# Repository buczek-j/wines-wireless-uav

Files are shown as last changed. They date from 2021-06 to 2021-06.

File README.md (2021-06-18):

# wines-wireless-uav
Public Repo for Publication "What is A Wireless UAV?A Design Blueprint for 6G Flying Wireless Nodes"



## Setup 
### UAV Parts list

The list of the off-the-shelf components used in the design of our UAV include:

* [Motors: T-Motor MN501-S KV240](https://store-en.tmotor.com/goods.php?id=695)
* [Propellers: T-Motor G20x6.5](https://store-en.tmotor.com/goods.php?id=496)
* [ESCs: T-Motor FLAME 60A 12S ](https://store-en.tmotor.com/goods.php?id=370)
* [Frame: Iflight iXC15 950mm](https://shop.iflight-rc.com/index.php?route=product/product&path=25&product_id=695)
* [Flight Controller: Holybro Pixhawk Mini](http://www.holybro.com/product/pixhawk-mini/)
* [Batteries: 4S 6000mAh (2 in series for 8s)](https://www.amazon.com/HOOVO-Connector-Airplane-Helicopter-Quadcopter/dp/B07PDPGFQY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)
* [Radio Reciever: FrSky XM+](https://www.amazon.com/FrSky-Range-Receiver-Failsafe-Support/dp/B073PXL55X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)
* [Radio Transmitter: FrSky Q9 Lite](https://www.amazon.com/FrSky-Transmitter-Protocol-Airplane-Helicopter/dp/B07RQ5BCNG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)
* [NUC: NUC7i7DNK1E](https://www.amazon.com/Intel-Business-Mini-Technology-BLKNUC7i7DNK1E/dp/B07BR7LK7C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)
* [Wireless USB Adapter](https://www.amazon.com/Panda-Wireless-PAU06-300Mbps-Adapter/dp/B00JDVRCI0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)
* [Router](https://www.amazon.com/Panda-Wireless-PAU06-300Mbps-Adapter/dp/B00JDVRCI0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)
* [SDR: USRP B210](https://www.ettus.com/all-products/ub210-kit/)
* [TPU 3D filament](https://www.amazon.com/PolyFlex-3-00-mm-750g-Yellow/dp/B00YXBO1UW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)
* [Nylon Bridge 3d filament](https://www.amazon.com/Printer-Filament-1-75mm-Dimensional-Accuracy/dp/B01MXDJ3IL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)
* [3D Printer](https://www.amazon.com/LulzBot-B07PFQQSR9-TAZ-Workhorse-Edition/dp/B07PFQQSR9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)

### Construction


### Nuc Setup

### Flight Code

The flight code used for these UAVs is located [here](https://github.com/buczek-j/BasicArducopter/tree/wines-powertest). It uses the Dronekit python library to connect to the UAV via Mavlink messages. 

## Design Validation
### UAV Endurance Testing
For the endurance testing, [this script](https://github.com/buczek-j/BasicArducopter/blob/wines-powertest/power_test.py) was used to automate the process. The enduracne test outlined in the script is shown below:

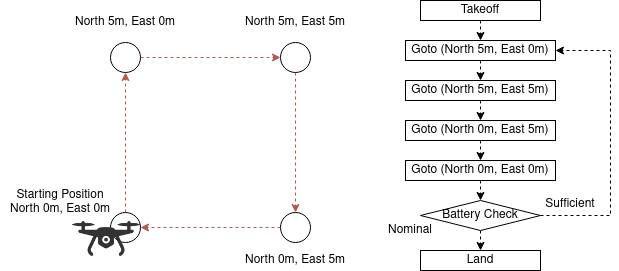
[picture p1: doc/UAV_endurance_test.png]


The UAV took off, performed a loop, and checked if its battery was below the 8S LiPo nominal voltage of 28.8V. If the voltage was below nominal, then the UAV would land, otherwise, it continued for another loop. The flight time and battery capacities were recorded and the capacities were confirmed via charging again. These values were used to calculate the total flight time of the UAV.

This process was repeated for multiple payload weights.

 This method of testing is more accurate to determine the flight time of a UAV as the UAV was contantly in motion. A flight test that would have the UAV hover in place would most likely dislpay an even longer flight time as the UAV would not need to adjust motor speeds for motion or altitude changes. 

### UAV GPS Interference
To determine the GPS interference caused by external electronics, the Pixhawk logs were analyzed. For each electronics and sheilding configuration, the UAV was armed on the ground, we waited until the desired time passed, and then the UAV was disarmed. The order of the configurations was recorded. After testing, the log files of the Pixhawk were [downloaded](https://ardupilot.org/copter/docs/common-downloading-and-analyzing-data-logs-in-mission-planner.html) from the UAV and using mission planner, .MAT files were generated from the logs. The .MAT files were parsed based on the Arming and Disarming messages and the Horizonal Dilution of Position (HDOP) of each configuration was separated. For our analysis, the HDOP recordings throughout each configuration's testing interval were averaged and the averaged HDOPs were compared. Four our testing, interval periods of 3 minutes were used. The script that we used to parse the .MAT files was [TODO]().

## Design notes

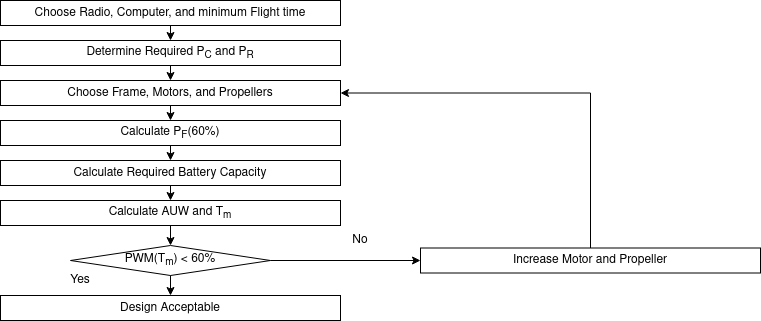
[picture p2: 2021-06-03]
doc/UAV_Deisgn_Process.png

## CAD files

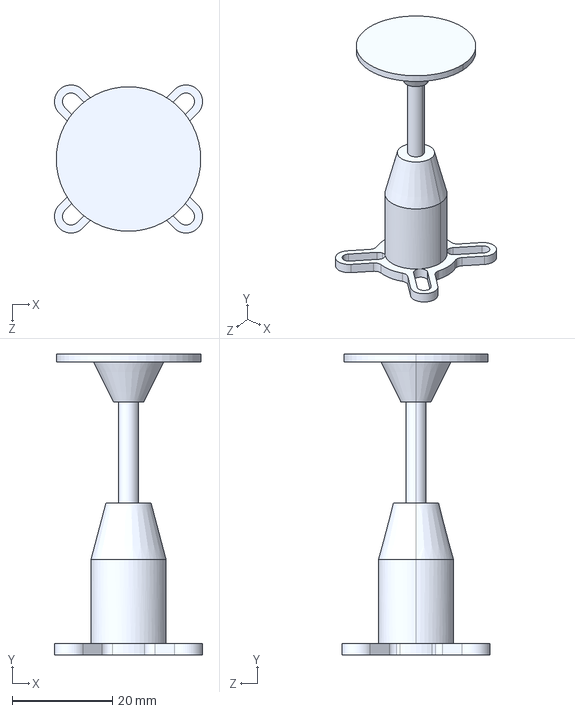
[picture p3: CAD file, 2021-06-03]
3D_Printed_Parts/Step_files/PX4_GPS_&_Compass_mast.STEP
29.5 x 60.0 x 29.5 mm

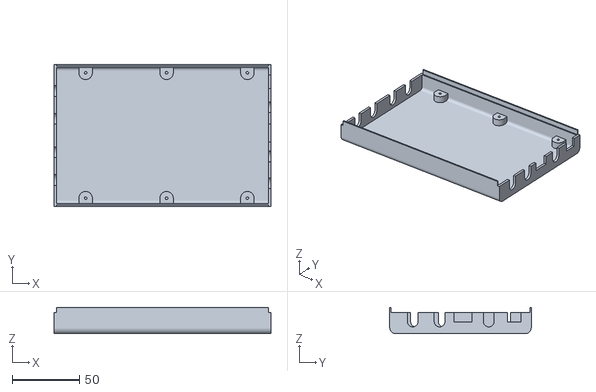
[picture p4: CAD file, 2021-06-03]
3D_Printed_Parts/STLs/bottom_case_b210.stl
161.0 x 105.0 x 19.5

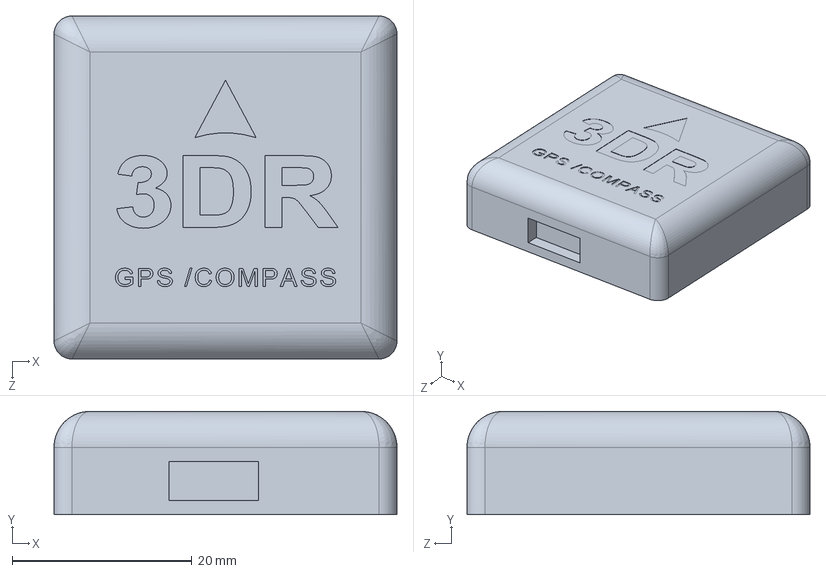
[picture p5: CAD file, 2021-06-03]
3D_Printed_Parts/Step_files/3DR_GPS_Compass.STEP
38.2 x 11.5 x 38.2 mm

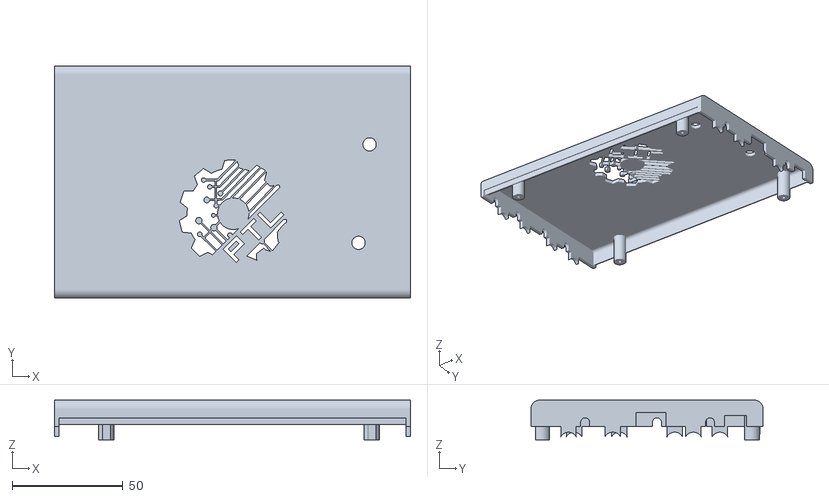
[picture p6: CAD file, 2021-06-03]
3D_Printed_Parts/STLs/top_case_b210.stl
161.0 x 105.0 x 18.0

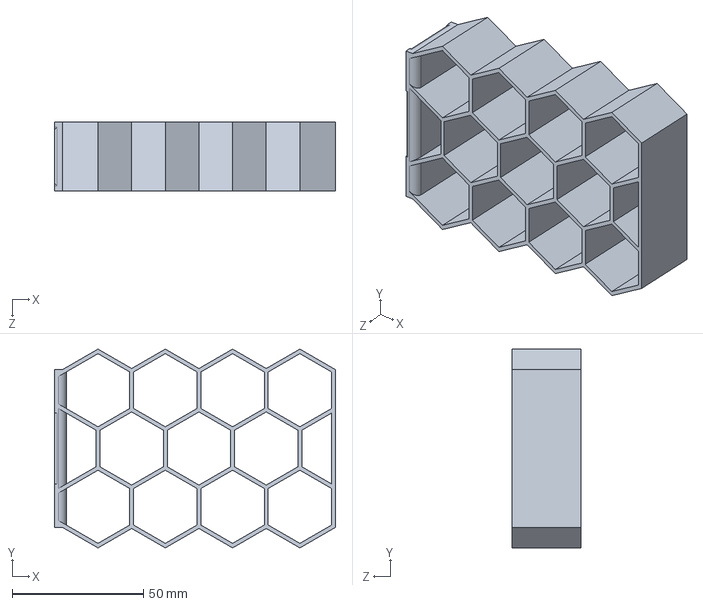
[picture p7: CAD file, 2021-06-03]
3D_Printed_Parts/Solidworks_parts/iflight_landing_gear_ziptie.SLDPRT
106.9 x 75.6 x 26.3 mm

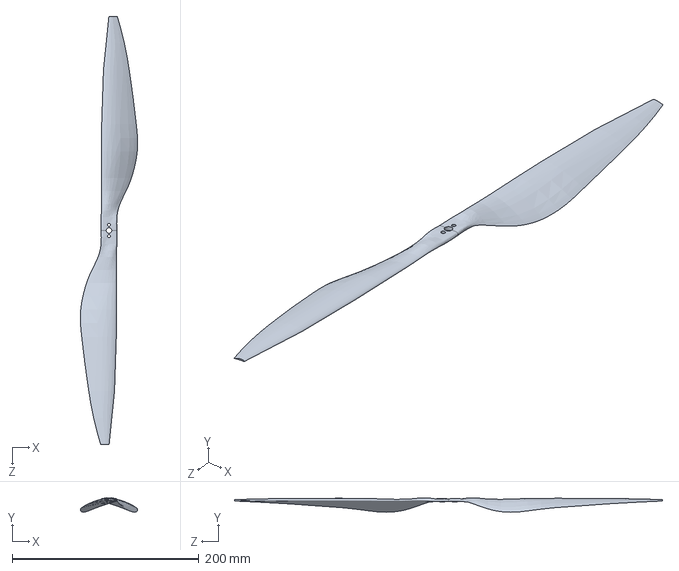
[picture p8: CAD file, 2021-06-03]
3D_Printed_Parts/Step_files/18x6.1.SLDPRT
61.4 x 15.5 x 458.0 mm

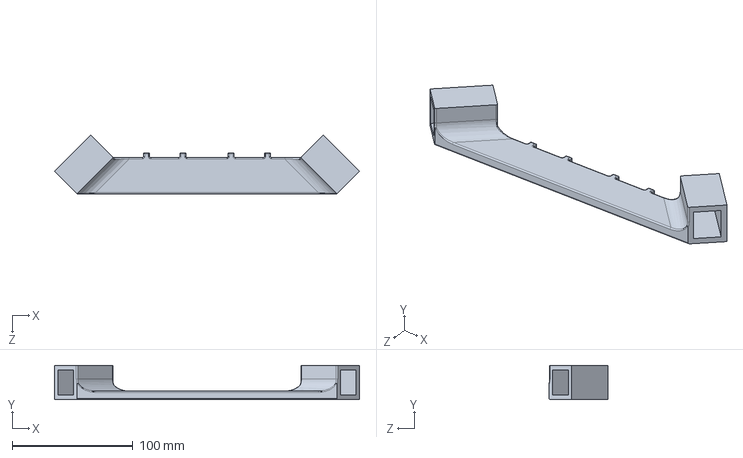
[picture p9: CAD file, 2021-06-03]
3D_Printed_Parts/Solidworks_parts/iflight_battery_mount.SLDPRT
252.3 x 28.3 x 48.7 mm

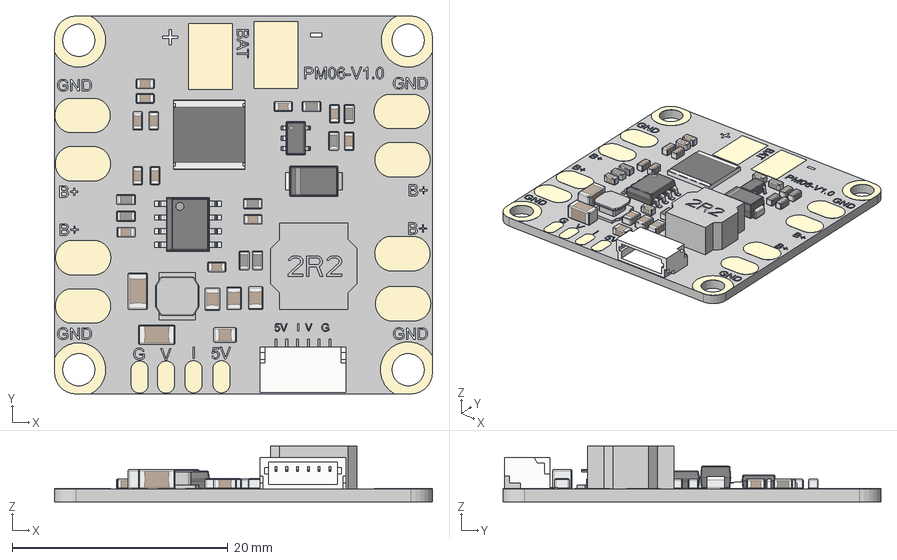
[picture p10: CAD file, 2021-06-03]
3D_Printed_Parts/Step_files/PM06.step
35.0 x 35.0 x 5.16 mm
CAPC-0603-T0.9-BN x 12
CAPC-0805-T0.95-BN x 4
CAPC-1206-T1.8-BN x 2
NTC-0603-T0.9 x 8
MS-012AA
SC-74A
DO-214AC-DIOM5127X23N
SRN8040TA
srn4018
SM06B-SRSS-TB
RESC-CUST

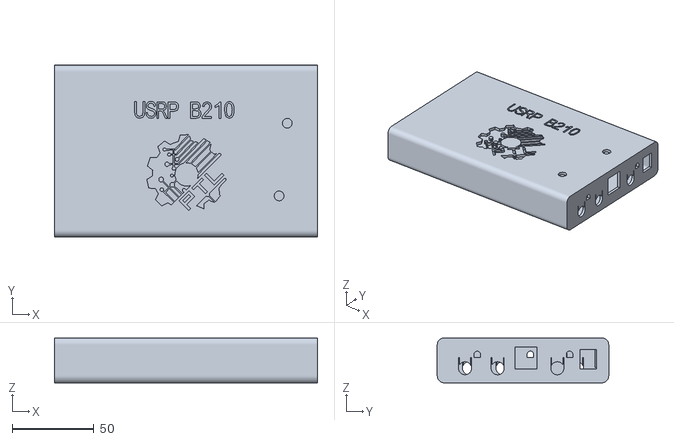
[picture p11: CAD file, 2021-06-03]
3D_Printed_Parts/Step_files/case_b210.stl
161.0 x 105.0 x 27.5

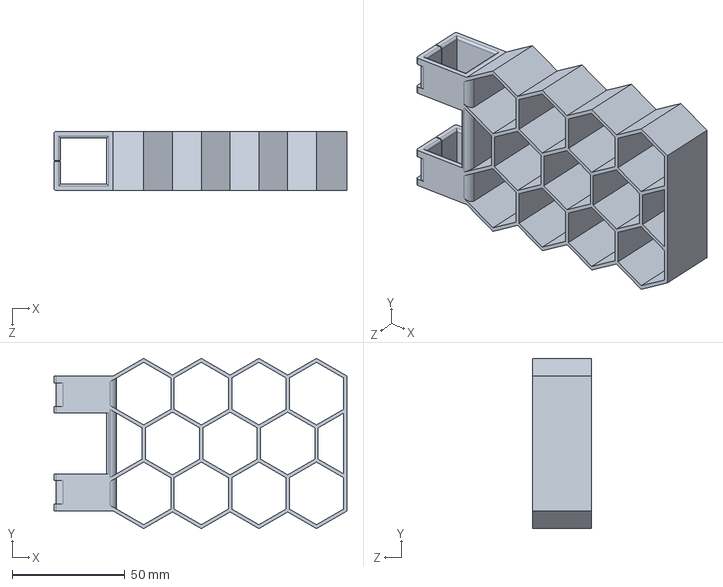
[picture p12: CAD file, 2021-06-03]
3D_Printed_Parts/Solidworks_parts/iflight_landing_gear.SLDPRT
130.2 x 75.6 x 26.3 mm

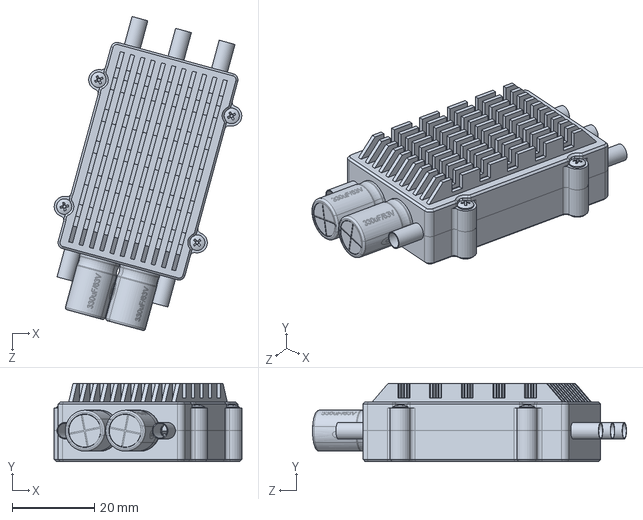
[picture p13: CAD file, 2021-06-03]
3D_Printed_Parts/Step_files/ESC_FLAME_60A_HV.SLDPRT
45.7 x 19.0 x 76.5 mm

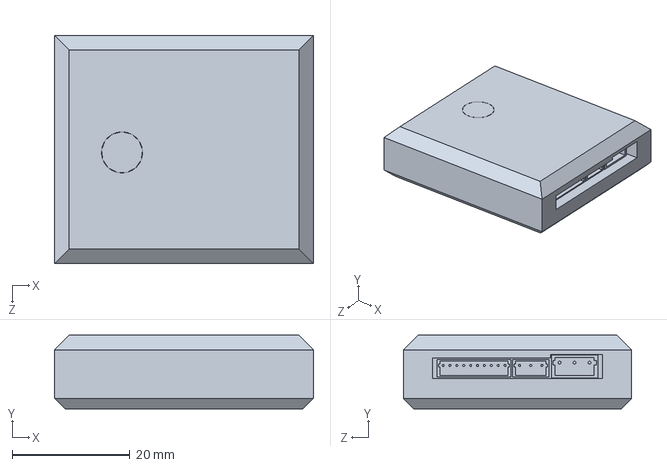
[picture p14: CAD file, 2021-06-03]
3D_Printed_Parts/Step_files/PixhawkMini.SLDPRT
44.0 x 12.5 x 38.8 mm

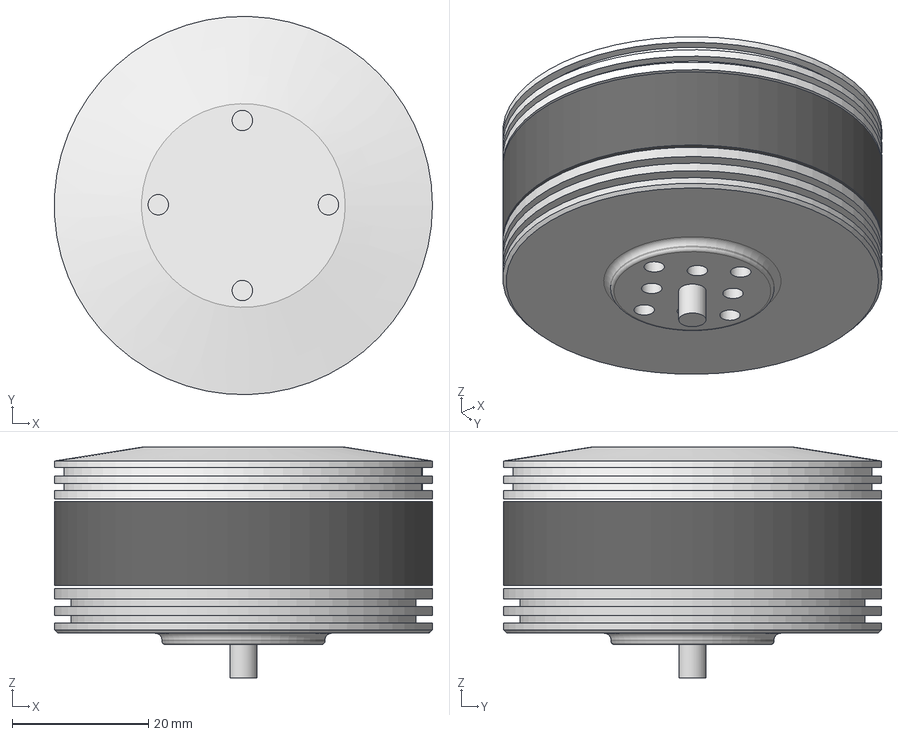
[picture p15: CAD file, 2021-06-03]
3D_Printed_Parts/Step_files/T motor MN501-S.step
55.6 x 55.6 x 33.9 mm
mn501s_top_001
mn501s_mid_001
mn501s_bot_001

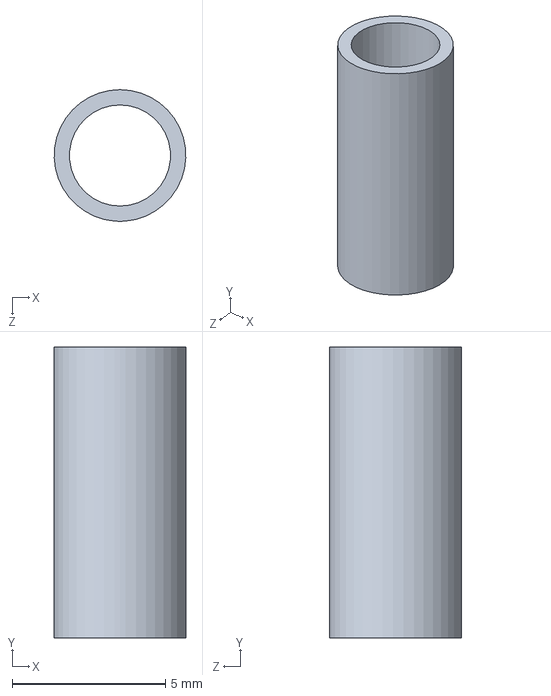
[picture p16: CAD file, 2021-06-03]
3D_Printed_Parts/Solidworks_parts/m3x9.5mm_standoff.SLDPRT
4.30 x 9.50 x 4.30 mm

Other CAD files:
3D_Printed_Parts/Solidworks_parts/m3x5mmx6mm_square_standoff.SLDPRT
3D_Printed_Parts/Solidworks_parts/m3x5mmx4.5mm_square_standoff.SLDPRT
3D_Printed_Parts/Solidworks_parts/m3x5mmx9mm_square_standoff.SLDPRT
3D_Printed_Parts/Solidworks_parts/m3x5mm_square_standoff.SLDPRT

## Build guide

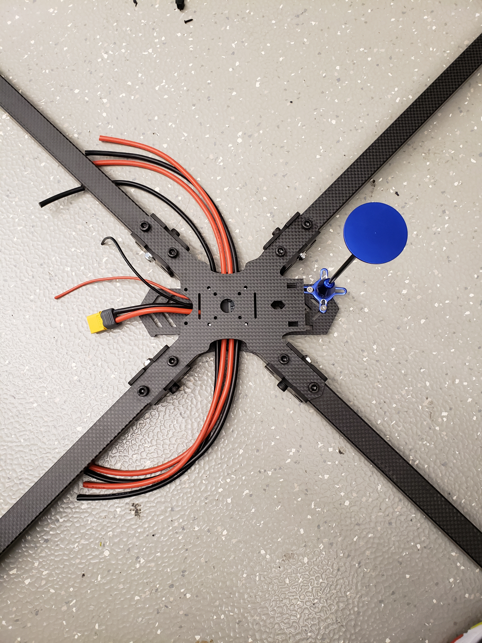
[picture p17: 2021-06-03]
doc/construction/20210406_110554.jpg

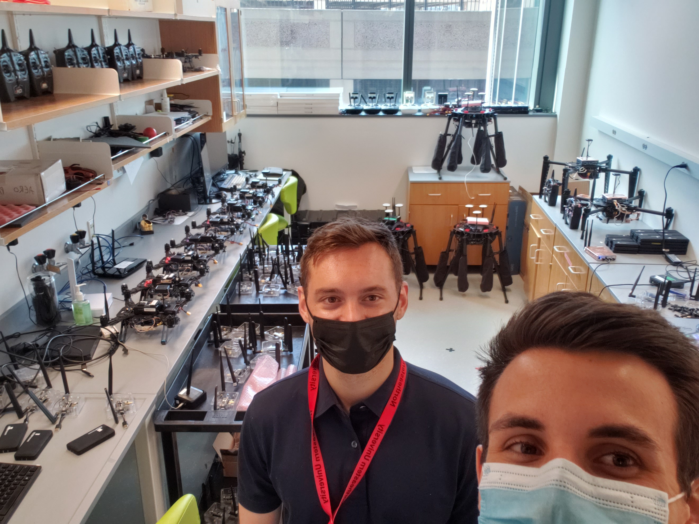
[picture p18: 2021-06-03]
doc/construction/20210506_094329.jpg

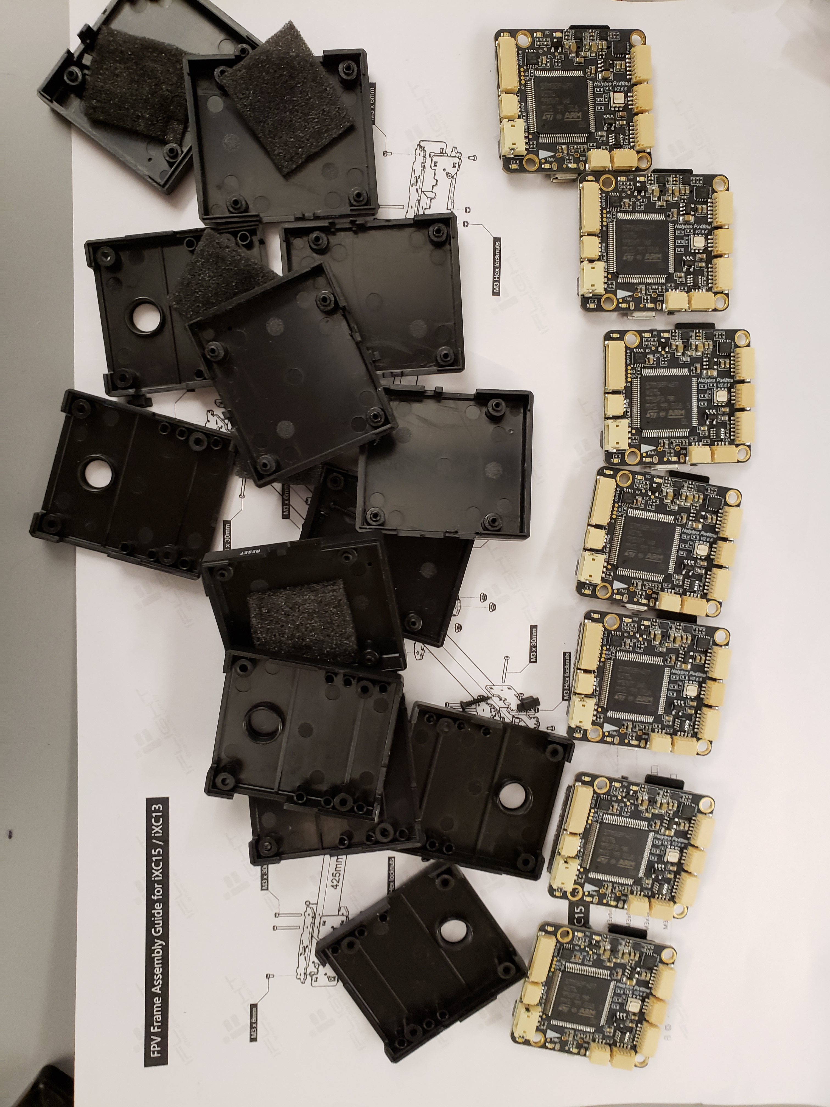
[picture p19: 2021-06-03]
doc/construction/20210405_161124.jpg

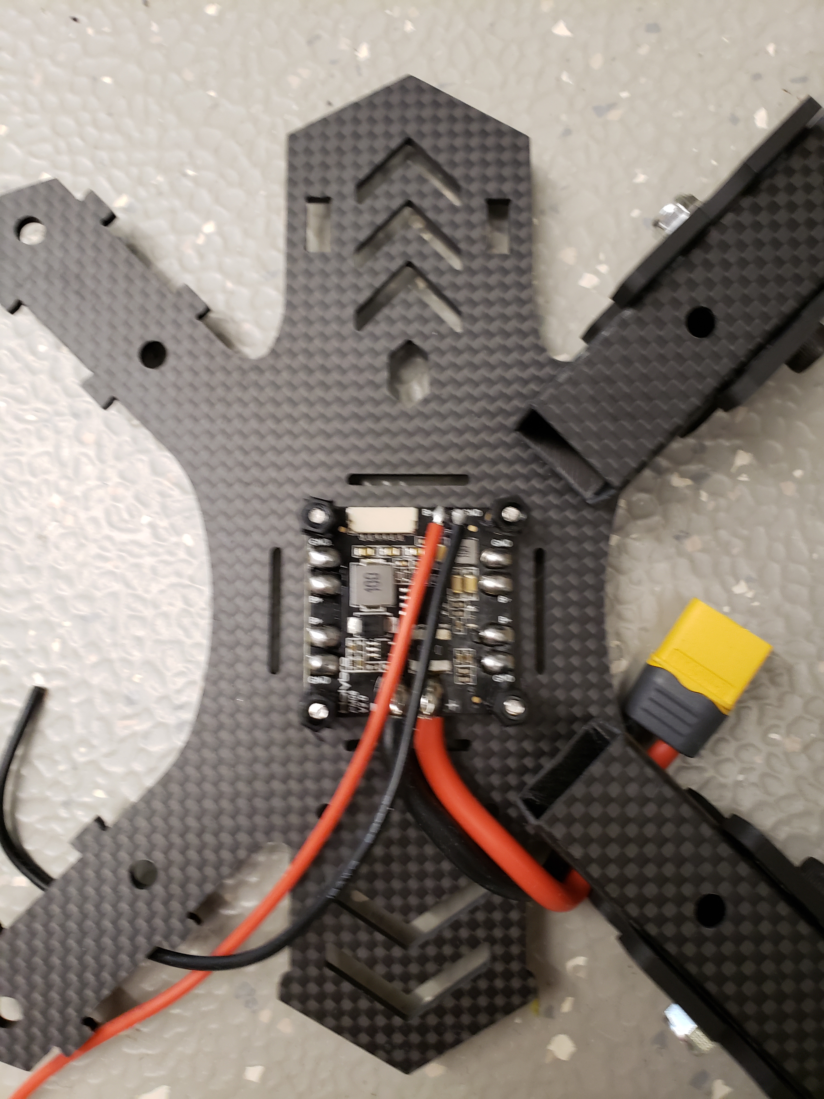
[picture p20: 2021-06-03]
doc/construction/20210406_110617.jpg

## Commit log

2021-06-03 added 3d prints
    [iflight_battery_mount.SLDPRT, iflight_landing_gear.SLDPRT, iflight_landing_gear_ziptie.SLDPRT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]
2021-06-03 added mn501 step file
    [T motor MN501-S.step]
2021-06-03 added other step files
    [18x6.1.SLDPRT, ESC_FLAME_60A_HV.SLDPRT, PM06.step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]
